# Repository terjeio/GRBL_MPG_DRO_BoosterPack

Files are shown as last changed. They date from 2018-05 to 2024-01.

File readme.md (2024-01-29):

## GRBL MPG & DRO BoosterPack for Tiva C \(TM4C123G\) and RP2040 (Pi Pico)

__2024-01-29:__ Added firmware and flasher code for the MSP430 keypad controller to the RP2040 version. This will check for and install/update the firmware automatically.  
Splitted LCD driver code in separate files for each display type supported.

__2022-01-13:__ Added wiring diagram for default key and LED map.

[Default wiring diagram (pdf)](media/Default%20keypad%20and%20LED%20wiring.pdf).  

The latest keypad code allows adding new keymappings at run time, switching between a few predefined ones or creating a new from scratch.

__2022-01-10:__ First preliminary version with Pi Pico support committed. Tiva C \(TM4C123\) version updated for new HAL/APIs.

__2021-08-30: Pi Pico breakout board design__

First batch of boards \(for final design verification\) to be ordered soon.

__2021-05-01: HALification of the code is underway__

A RP2040 driver for [Pi Pico](https://www.raspberrypi.org/products/raspberry-pi-pico/) is nearing completion, watch this space.

__2019-08-20: Improved startup sequence__

The GPIO line used for signalling MPG mode change is now used to signal the grbl controller ready state during startup.

On a cold start the Grbl microcontroller should pull the line low as early in the process as possible.
When the cold start sequence is completed and grbl is ready to receive data the line should be reverted to input mode with interrupt and pullup enabled.
The MPG microcontroller will wait for the line going high before starting any communication, displaying a progress indicator in its boot screen while waiting.

---

Features:

* SPI LCD and touch interface
* Up to two MPG wheels (QEI connected)
* Four GPIO pins, one is preassigned for switching grbl to/from MPG mode
* Up to 8 LEDs, buffered open drain 
* Feed Hold and Cycle Start outputs, open drain
* Up to 25 keys (in matrix)
* Navigator interface
* I2C port (3V3)
* On board MSP430G2553 handling keys and LEDs, internal I2C interface to Tiva C

Parts of alpha-version of supporting code is now available.
An initial commit of the [display driver](https://github.com/terjeio/Display-libraries/) used has now been made public.
The code is written so it is should be easy to port, all processor dependent code is in separate files. 

All core funtionality is now up and running, GUI is 100% event driven making it easy to extend with new dialogs. Shared dialogs (canvases) created for common data (such as DOC, feed rate, RPM), input review/confirmation and GCode transfer to grbl.

### How it works

The setup comprises 3 microcontrollers: one running Grbl, one handling the keyboard scanning and one (the MPG processor) for the DRO and MPG \(user interface\).

#### Grbl/grblHAL microcontroller:

Support for a second input stream and a switch for changing to/from MPG mode has to be added to the code.
In \"normal\" mode the MPG processor listen to the output stream from Grbl, parses the data and displays relevant info on the display.
In \"MPG\" mode Grbl switches its serial input to the second input stream and the MPG prosessor takes over control by acting as a GCode sender.
To tell the MPG processor about a mode change the real time report from Grbl is extended with |MPG:0 \(\"normal\"\) and |MPG:1 \(\"MPG\"\), this is only added when the mode change takes place.
Some of my [grblHAL drivers](https://github.com/grblHAL) supports this functionality as does my [patched version of grbl-Mega](https://github.com/terjeio/grbl-Mega).
 
#### MPG microcontroller:

This handles the user interface \(keypresses, MPG input, menu navigator input and DRO display\). In \"normal\" mode it passively listen to the output stream coming from Grbl, parses it and updates the display and LED statuses accordingly.
For this to work correctly there has to be a PC based GCode sender connected to the controller, such as [ioSender](https://github.com/terjeio/ioSender), that constantly request the real time status report.

In \"MPG\" mode it takes over control and acts as a GCode sender itself, ideally the PC based GCode sender should then disable its GUI.
When turning the MPG wheels G1 commands are issued with a feed rate that is dependent on the turning speed, simulating the action of the handwheels on the lathe.
The jog buttons issues jog commands and most of the other buttons issues real-time commands such as Hold or Cycle start. It is also possible to hardwire some of the button states to the corresponding Grbl input signals.

For the lathe version I am currently working on I am adding canvases \(or dialogs\) that will be used for some simple tasks such as reducing the diameter of the stock, and possibly threading if the Grbl version supports that.
There is a common canvas for streaming task data, this may be used to stream data from a SD card \(not yet implemented\). 

#### Keyboard handling microcontroller:

Due to limited IO on the MPG microcontroller a separate processor is employed for handling the keyboard and LEDs.
Up to 25 keys can be added (in a matrix) and 8 LEDs are supported. Keypresses are sent to the MPG controller via I2C, and there is a strobe signal for telling MPG controller that a key is pressed.
The strobe signal suppports different key modes such as single shot, autorepeat and continuous - configurable per key.

---

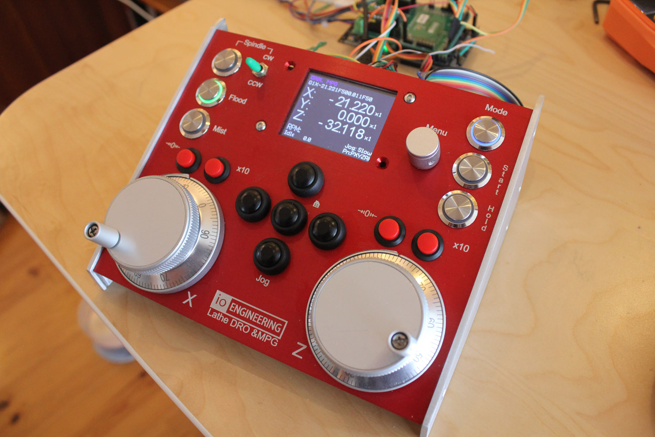
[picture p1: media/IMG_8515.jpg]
Testbench setup


### Pi Pico breakout board

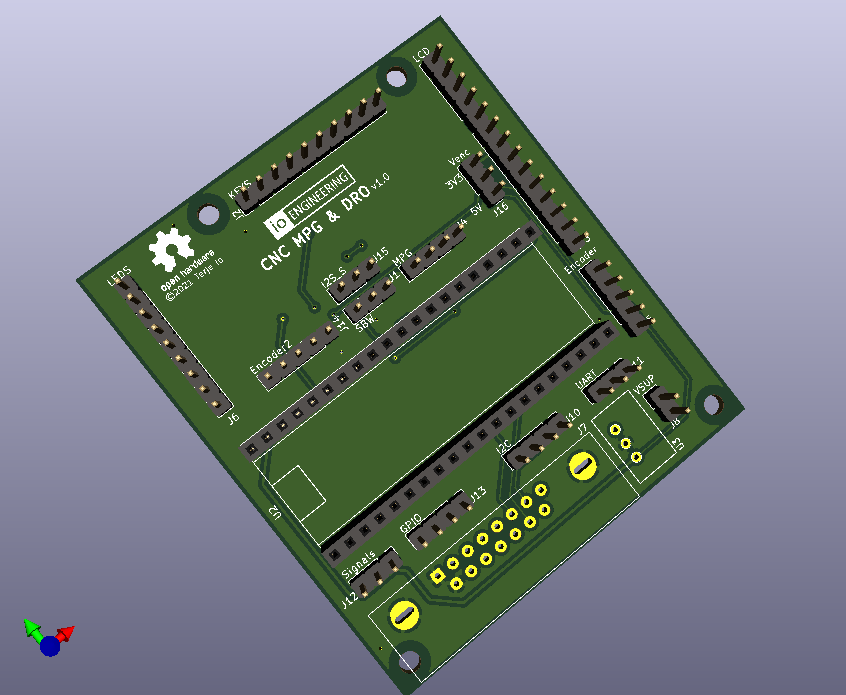
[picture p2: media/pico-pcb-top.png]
Pico PCB top

 
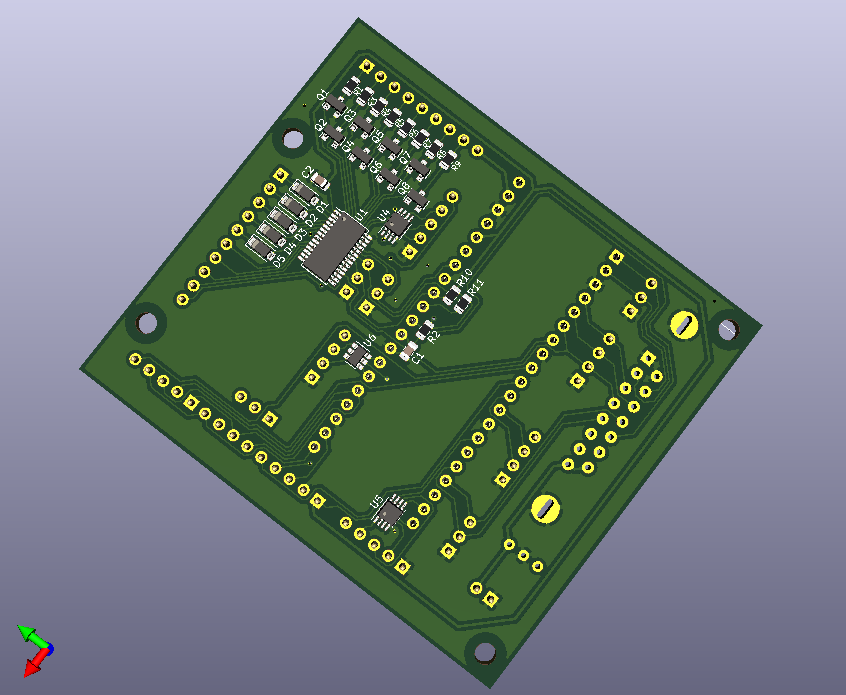
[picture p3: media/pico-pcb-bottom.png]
Pico PCB bottom


---
2021-08-30

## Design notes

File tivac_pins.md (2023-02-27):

#### LaunchPad pin assignments:

``` plain
                   3v3 [] [] VBUS (P14.1)                             PF2 [] [] GND
                   PB5 [] [] GND                         GPIO1 (P2.4) PF3 [] [] PB2 GPIO3 (P2.2)
    UART RX (P3.3) PB0 [] [] PD0 I2SCL (P10.3)           GPIO2 (P2.3) PB3 [] [] PE0 Cycle start (P8.2)
    UART TX (P3.2) PB1 [] [] PD1 I2SDA (P10.3)          Keypad strobe PC4 [] [] PF0 QEI0 (P6.3)
                   PE4 [] [] PD2 GPIO6 (P10.4)          QEI1 A (P9.3) PC5 [] [] RST
                   PE5 [] [] PD3 DISPLAY CS (P13.7)     QEI1 B (P9.2) PC6 [] [] PB7 MOSI (P13.4, P12.3?)
SCK (P12.5, P13.3) PB4 [] [] PE1 Feed hold (P8.3) Navigator SW (P5.4) PC7 [] [] PB6 SIMO (P13.1, P12.2?)
       D/C (P13.5) PA5 [] [] PE2 TOUCH CS (P12.4)   Navigator+ (P5.3) PD6 [] [] PA4
            I2CSCL PA6 [] [] PE3 TOUCH IRQ (P12.1)  Navigator- (P5.2) PD7 [] [] PA3
            I2CSDA PA7 [] [] PF1 QEI0 B (P6.2)           RESET (P13.6)PF4 [] [] PA2

GND: P2.1, P3.1, P5.1, P8.1, P10.1, P13.8
3V3: P5.5, P6.5, P9.4, P13.2, P13.9
 
```

#### Tiva connected socket/pins:

GPIO \(P2\):

```
GND   GND P2.1
GPIO3 PB2 P2.2
GPIO2 PB3 P2.3
GPIO1 PF3 P2.4
```

UART \(P3\):

```
GND GND P3.1
TX  PB1 P3.2
RX  PB0 P3.3
```

Navigator \(P5\):

```
GND GND P5.1
-   PD7 P5.2
+   PD6 P5.3
SW  PC7 P5.4
```

MPG0 \(P6)\:

```
GND GND P6.1
+   PF1 P6.2
-   PF0 P6.3
3V3 3V3 P6.4
```

Signals, open drain \(P8\):

```
GND         GND P8.1
Cycle Start PE0 P8.2
Feed Hold   PE1 P8.3
```

MPG0 \(P9\):

```
GND GND P9.1
+   PC6 P9.2
-   PC7 P9.3
3V3 3V3 P9.4
```

I2C \(P10\):

```
GND GND P10.1
SDA PD1 P10.2
SCL PD0 P10.3
IRQ PD2 P10.4 (I2C Strobe signal)
NC  --- P10.5
```

LCD Touch Sensor \(P12\):

```
T_IRQ PE3 P12.1
T_DO  PB7 P12.2 (MISO)
T_DIN PB6 P12.3 (MOSI)
T_CS  PE2 P12.4
T_CLK PB4 P12.5
```

LCD Display (P13):

```
SDO   PB6 P13.1 (MISO)
LED   3v3 P13.2
SCK   PB4 P13.3
SDI   PB7 P13.4 (MOSI)
D/C   PA5 P13.5
RESET PF4 P13.6
CS    PD3 P13.7
GND   GND P13.8
VCC   3V3 P13.9
```

---

#### MSP430G2553 connected socket/pins:

Keypad matrix interface \(P11\):

```
ROW0 P11.1  P1.0
ROW1 P11.2  P1.1
ROW2 P11.3  P1.2
ROW3 P11.4  P1.3
ROW4 P11.5  P1.4
COL0 P11.6  P2.0
COL1 P11.7  P2.1
COL2 P11.8  P2.2
COL3 P11.9  P2.3
COL4 P11.10 P2.4
```

LEDs, open drain \(P14\):

```
LED0 P14.8 P3.0
LED1 P14.9 P3.1
LED2 P14.7 P3.2
LED3 P14.6 P3.3
LED4 P14.5 P3.4
LED5 P14.4 P3.5
LED6 P14.3 P3.6
LED7 P14.2 P3.7
+5V  P14.1
```

SWD - MSP430 programming interface \(P4\):

```
GND  P4.1
TEST P4.2
RST  P4.3
```

---

#### Internal keypad interface to Tiva MCU:

```
P1.6 I2CSCL        PA6
P1.7 I2CSDA        PA7
P2.5 Keypad strobe PC4
```

---
2023-02-27

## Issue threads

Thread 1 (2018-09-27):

Congratulations!, great job!

luisluna2, 2018-09-27:
Hello friend just now I¿'m working in a similar project, but I wenna usa  a SD card but not have success with this.

I make  a code with LCD 1602 I2C and now the machine can move but the problem is how send data from SD CARD, have some about this?

terjeio, 2018-09-27:
Thanks,

Funny you should mention SD card now, I just looked into how to hook code for streaming data from a SD card into my grbl port a few hours ago. So far I just added the hook, no code yet for interacting with the card.

 I have also added added code (not yet published) for streaming GCode via ethernet to the driver for the [EK-TM4C1294XL LaunchPad](https://github.com/terjeio/grblHAL/tree/master/drivers/TM4C129), this ment that I had to run grbl as a FreeRTOS task - in a similar vein as the ESP32 port found [here](https://github.com/bdring/Grbl_Esp32). The ESP32 port support for streaming from a SD card, maybe that implementation can give you some ideas?

Do you use a second microcontroller for your solution too?

luisluna2, 2018-09-27:
wow! good job!, could send some picture for undertand more?, sorry I'm new in Arduino hehe

terjeio, 2018-09-28:
@luisluna2 I have added some details about my setup to the readme that may be helpful. Implementing the setup you describe on a single microprocessor is IMO not going to be easy, the Arduino Nano surely does not have enough free resources for that. Perhaps the way forward will be to use your Mega as the Grbl controller, this with my patched version, and implement the DRO/MPG and SD card support on the Nano?

I do not work with Arduino controllers, my expertise is with TIs 16 bit controllers and ARM processors, so I can not offer much help for Arduinos. Maybe switching to the ESP32 I mentioned above is a better choice for your ambitions, but it still needs a second processor for some parts (such as keyboard input) as it has limited IO resources. Or you could adapt this project if you feel so inclined...

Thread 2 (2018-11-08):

3 or 4 wheels

jschoch, 2018-11-08:
I'm working on a similar project but with 3 or 4 wheels.  STM32 can support 4 hardware quadrature pulse counters.  Wondering if this is something you have considered?  Also wondering how the physical interface is to use with your layout.  Any lessons learned on the physical UI?

terjeio, 2018-11-08:
Not sure what you mean, but I will try to answer.
I have not considered using STM32 processors, I mainly work with Texas Instrument processors. However, I try to write my code in a layered manner so that hardware dependencies are implemented in separate files from the main application - as a HAL (Hardware Abstraction Layer). This allows for clean porting to different platforms. If you meant support for more than 2 wheels then I have not considered that but it should be fairly easy to add to my code. It could also be done by a single wheel and an axis selector switch.

Again, not sure what you mean by lessons learned from the physical UI - you mean the complete layout with the LCD, MPG wheels, menu navigator and buttons? If so then I am happy with it as it is aimed at controlling my small lathe. It would be nice to have a complete numerical keypad for data entry - but that would result in a much larger device. So I decided to use a MPG wheel in combination with the jog buttons and meny navigator for data entry to keep the size down. One issue on my todo list is to change the input fields for numerical values to right justified - I need to update the UI library for that.
The LCD is touch sensitive and the UI library supports touch input, currently this is not enabled in my code, I will add that it later to see how it works out as an alternative to the menu navigator.

jschoch, 2018-11-09:
This helps.  I made a bad assumption you were using this for a mill style machine.

I want to have X, Y, Z, and Feed jog wheels all available.  X would be "front", Y "right", Z "top", and "feed" left laid out on a cube.

I was also asking about your hardware input device layout, how you like it, and what lessons you learned designing it.  Sounds like you are pleased with the  physical input layout for a lathe.  Could you use it for a mill?

terjeio, 2018-11-09:
> Could you use it for a mill?

Short answer: the physical design, no - the software yes.

For a mill I think I would reduce the design to a single MPG wheel and an axis selector switch - I believe this is the most common configuration for mills. But then your use-case may be different.

I like the jog buttons so I would add two for the Z-axis as I have done for my CO2-laser. The keyboard scanning code supports two-key rollover which I use for jogging X and Y simultaneously.

Perhaps a numeric keypad for data entry would be more useful than three MPG wheels? Depends on how advanced and easy-to-use one wants the software to be.

Whatever the physical design chosen I believe the core software can, IMO, be easily adapted to support it.

Using a MPG wheel for feed is perhaps an overkill, when in DRO mode I use the menu navigator for adjusting the spindle RPM, it could be used for feed as well. Be aware that when turning the MPG wheels I do not issue jog commands - I prefer to issue G1 commands with feed rate proportional to the turning speed to move the axes to the exact position as indicated by the wheel dial or the DRO. When turning the wheels the DRO position changes color to indicate target position is shown, not the current as reported by Grbl.

terjeio, 2018-11-11:
I use short key presses on the "Home key" in the center of the jog buttons to toggle between fast, slow and step mode jogging. In my GCode sender I use <SHIFT> and <CTRL> as jog modifiers in a similar way. Since I have (IMO) fixed the jog cancel "bug" I issue "long" jog commands in fast and slow modes and relies on the jog cancel command to terminate a running jog movement. This means that I do not rely on any feedback other than the current state for the action taken.

For the G1 commands I rely on the speed of the MPG wheel to calculate the feed rate - I get the velocity from a register in the processor. The formula to calulate the feed rate can be found in the source code (canvas/dro.c and mpg.c). The way I handle the MPG input is in a way a "set and go" mode as you describe it - in an interactive way. The target position is displayed in the DRO while a wheel is turned - also the dial (or scale?) on the wheel may be used, there is a button for aligning this dial with the DRO display.

Perhaps [this video snippet](https://www.youtube.com/watch?v=_0Nmh164dvo) may shed some light on how it works?

terjeio, 2018-11-11:
> The colored position is the cumulative target?

I guess you can say so, it is the absolute position where the controlled point (the tool) will stop if one stop turning the handwheel. It is still early days for me in terms of usage, so far I like to look at the DRO for approaching the target and then often the dial markings (or whatever they are called for) on the wheels for the final adjustment. I have started to write some canvases (or screens) for data entry for some simple tasks,  I guess that is nice to have for better surface finish and, for a mill, stuff that is hard/impossible to do manually but not complicated enough to warrant making a proper Gcode program.

>  Did you consider displaying both current and target?

Could do but so far I did not feel I need it, it is also a question of available screen real estate and avoiding clutter in the display. Also at x1 mode the controlled point does not lag much behind - turning a MPG wheel is kind of similar to turning a physical handwheel (that is my design aim). That said, I am no machinist - I am an electronics engineer/programmer making CNC stuff as a hobby so what do I know...
The nice thing about making my own design and writing the code is that I can change stuff to my liking :-)
>  If so why did you choose a single position display?

See above, may well change it later as the data is a few display calls away.

Having this discussion here is no problem for me, I - and others - may learn something from the discussion as well.

terjeio, 2018-12-03:
MPG wheels: bounce (if any) not an issue, I guess the QEI module in the processor takes care of any since I have enabled filtering by calling QEIFilterEnable. I have not tried with filtering disabled.

Menu navigator encoder:  bounces badly - added software debounce to fix that. RC-filters should help but I did not add them, slow opto-couplers can also act as debouncers. I have used MAX6816 for debouncing input to a CPLD in another project - a bit expensive but reliable, perhaps debounce duration is too long for an encoder? MAX6817 is the dual input version.

Optical encoders should IMO produce a clean signal, but may still cause bounce if the inputs are not schmitt triggered. Output from a optical encoder may in fact be considered analog if output is not preconditioned to be digital. Digital in this context meaning the output having a constant rise/fall time regardless of speed.

jschoch, 2018-12-06:
thanks for the response again.

I'm way down the rabbit hole on this now. I thought it would be much simpler but i'm learning a lot.

Right now i'm stuck deciding how to handle state transitions.  I think your code will calculate the delta to the target position and wait for that position to allow more input from the encoders.  Did you consider issuing the jog and then watching the states transition Idle -> Jog -> Idle?  I can see a possibility where I miss a transition and then never can accept new jog inputs.

 I suppose the only reason not to calculate the target position is some small saving in that calculation, perhaps I need to track these transitions to fully utilize CMD_JOG_CANCEL, but now that i'm thinking though the state transition monitoring I can't see any good reason it would be better with open loop control.  For closed loop there may be some reason you'd never get to the target position.  Wondering what your thinking was on when to block additional jog inputs.

I also generalized your grblcomm stuff into an arduino library here:  https://github.com/jschoch/grbl_chat
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
terjeio, 2018-12-06:
I issue "normal" G1 commands when movement is commanded via the MPG wheels, not jog commands - so there is no jog cancel involved.

What may be hard to infer from my code is that it is completely event driven. The EventNullEvent trapped in canvasHandler() in dro.c will happen every 10mS, I use that to flag when the display should be updated and the mpg input should be checked. Currently the display update is set to 20 ticks (200ms) and mpg input to 10 ticks (100ms).

In my main() function you will see it ends with 3 calls in a while(true) loop, the those calls would go in the loop() function if the same approach was used for Arduino.

MPG_Move() thus gets called every 100ms, which gets MPG wheel positions from the QEI module and compares them to a local copy, if different the delta is computed and used for calculating the target position.

I do not rely on state transitions from grbl to handle MPG movement, as long as the wheels are turned I will issue G1 commands (every 100mS). A state change back to "normal" is when there was no change in MPG positions during the last 100mS period.

To be able to do this I need to set a reference position (current position from grbl, mpg_base), to update this I rely on a state change to Idle - see displayGrblData() where I call MPG_ResetPosition(). Also offset changes is taken care of as well as setting the reference position at startup.

How this could be adapted to issue jog commands instead in a good way I do not know. Do you just want to continue issuing jog commands until wheel movement stops and then issue a jog cancel? Or only cancel on a direction change?

As for the "bug" in parseFeedSpeed that is due to I change I have made to the real-time report, I have added a third parameter - the actual spindle speed.  This one should work:

```
static void parseFeedSpeed (char *data)
{
    char *next;

    next = strchr(data, ',');
    *next++ = '\0';

    if(parseDecimal(&grbl_data.feed_rate, data))
        grbl_data.changed.feed = true;

    if(parseDecimal(&grbl_data.spindle.rpm_programmed, next))
        grbl_data.changed.rpm = true;

}
```

I hope this helps, if not just continue asking.

jschoch, 2018-12-06:
thanks again, this is great feedback.

> How this could be adapted to issue jog commands instead in a good way I do not know. Do you just > want to continue issuing jog commands until wheel movement stops and then issue a jog cancel? Or > only cancel on a direction change?

The two modes i'm considering are single step, and acceleration based "batch step".  The latter might benefit from jog_cancel since I want to have the grbl planner accelerate based on the wheel velocity and time it has been turning.  My idea was to mark the wheel turning with a flag when it starts turning and then if the wheel had been turning and stopped to issue the jog_cancel and to halt all other input to grbl.  I see that folks try to just stop issuing more jog commands rather than trying to use CMD_JOG_CANCEL due to the potential race condition.  I've not yet been able to get something that works smoothly and avoids odd states and I'm actually focused on getting the first cast working safely and atomically.

Right now I'm processing the encoder wheel updates very quickly (by mistake) and I likely am creating more problems for my self that way.  The current version issues a "?" query after the jog and I notice that I can issue and receive "ok" for 2 or 3 jog commands before the state changes to a Jog state.  reducing  encoder wheel input polling time is a pretty easy way to get more control over things.

my next refactor will try to model things based on a finite state machine.  I will pay closer attention to polling intervals and start to calculate target positions.

Closed 2020-02-04.

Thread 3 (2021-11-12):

Possible to buy an PIPico pcb?

mundsen, 2021-11-12:
Cool project

terjeio, 2021-11-13:
I have to order some PCBs first - been too busy to do that. I have one homemade prototype (single-sided) so hopefully the first run will be bug-free...

mundsen, 2021-11-13:
ok :-)

Have ordered a Tiva C , LCD and Pico

As a first step I hope to get the LCD working in combination with my grblHAL Pro

terjeio, 2021-11-13:
The Tiva C is not needed, the Pico is used as an alternative...

There is a MSP430 on the board that needs to be programmed, my plan is to port the programming code (it is public domain) so that the Pico can do that.
Currently I use a MSP-EXP430G2 to program it, it is possible that the Tiva C can be used as well. Anyway, I believe can supply a preprogrammed MSP430 - IIRC I have an adaptor for doing that off PCB.

terjeio, 2022-01-05:
FYI I have now received a few PCBs and have the first up and running with basic functionality in place.
I need to make a 5x5 keypad to assign and check out new key mappings required as the board only support a single MPG encoder so there is a little bit more work to do before I can release the code.

You still want a PCB? Unpopulated?

mundsen, 2022-01-05:
Yes 😊

Would like to test it with my laser project based on the grblHAL Teensy 4.1 Pro controller [Image.jpeg]

Last ned Outlook for iOS<https://aka.ms/o0ukef>
________________________________
Fra: Terje Io ***@***.***>
Sendt: Wednesday, January 5, 2022 9:07:33 PM
Til: terjeio/GRBL_MPG_DRO_BoosterPack ***@***.***>
Kopi: Øyvind Amundsen ***@***.***>; Author ***@***.***>
Emne: Re: [terjeio/GRBL_MPG_DRO_BoosterPack] Possible to buy an PIPico pcb? (Issue #3)

FYI I have now received a few PCBs and have the first up and running with basic functionality in place.
I need to make a 5x5 keypad to assign and check out new key mappings required as the board only support a single MPG encoder so there is a little bit more work to do before I can release the code.

You still want a PCB? Unpopulated?

—
Reply to this email directly, view it on GitHub<https://github.com/terjeio/GRBL_MPG_DRO_BoosterPack/issues/3#issuecomment-1006040344>, or unsubscribe<https://github.com/notifications/unsubscribe-auth/AAXKXEKX45N3P5TTZ366LMDUUSQILANCNFSM5H47LWKA>.
You are receiving this because you authored the thread.Message ID: ***@***.***>

mundsen, 2022-01-08:
Is Grbl v1.1 jogging supported by grblHAL ?

https://github.com/gnea/grbl/wiki/Grbl-v1.1-Jogging

terjeio, 2022-01-08:
> Is Grbl v1.1 jogging supported by grblHAL ?

Yes, and I have fixed the bug where a jog cancel is sometimes not handled as it should.

Also, legacy Grbl errors out if a jog command exceeds max travel if soft limits is enabled - contrary to what the linked document claims. grblHAL has separate soft limits handling for jog commands that can be enabled by setting $40 to 1.

terjeio, 2022-01-13:
Testing is going well and I have ordered an adaptor for programming the MSP430 off board. Should be here soon.

Here is the BOM as extracted from KiCad:

[RP2040 MPG and DRO.zip](https://github.com/terjeio/GRBL_MPG_DRO_BoosterPack/files/7860577/RP2040.MPG.and.DRO.zip)

R1-9 has no value due to LEDs often having different current requirements for outputting the same brigthness. I use 2K7 for the 3mm LEDs in my test setup and the different colors vary from quite dim to very bright...
R1-9 could be replaced with 0R resistors on the board and having leaded resistors in series with the LEDs instead.

U3 is not needed if the supply voltage is 5V or the Pico is connected via USB. Short pin 1 and 3 with a wire if so.

DB15 is optional, use the connector(s) of your choice and wire to the pin headers as needed. I believe that wireless operation via HC-05 bluetooth modules is possble but I have not tested that yet.

The display is a [2.4" ILI9341 based panel](https://www.ebay.co.uk/sch/i.html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), I may add touch support later but not sure if it is going to be practical.

My test setup has all 25 buttons wired up, do you plan to add any? ([You will need at least two](https://github.com/terjeio/GRBL_MPG_DRO_BoosterPack/discussions/6#discussion-3786872)).

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

mundsen, 2022-01-13:
Possible to use something like this?

https://www.aliexpress.com/item/32635207928.html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,scm-url:1007.13339.169870.0,pvid:af4624f1-85fd-40f5-8538-35733463f9a3,tpp_buckets:668%232846%238111%231996&&pdp_ext_f=%7B%22sceneId%22:%223339%22,%22sku_id%22:%2210000006002568188%22%7D

less wires - Seems like different keys gives different ohm values?

terjeio, 2022-01-13:
> Possible to use something like this?

Yes, but you will have to write code for it. Polling an AD-converter and decoding the value. You can ditch the MSP430 if doing that - and luckily the I2C SDA/SDC going to it are broken out to a pin header. Depending on how many key functions you require it may be a bit restrictive though - and I am not sure you will be able to get two key rollover to work.

mundsen, 2022-01-13:
Ok only an idea - I guess it’s best start with the same setup you use

Last ned Outlook for iOS<https://aka.ms/o0ukef>
________________________________
Fra: Terje Io ***@***.***>
Sendt: Thursday, January 13, 2022 10:01:49 PM
Til: terjeio/GRBL_MPG_DRO_BoosterPack ***@***.***>
Kopi: Øyvind Amundsen ***@***.***>; Author ***@***.***>
Emne: Re: [terjeio/GRBL_MPG_DRO_BoosterPack] Possible to buy an PIPico pcb? (Issue #3)

Possible to use something like this?

Yes, but you will have to write code for it. Polling an AD-converter and decoding the value. You can ditch the MSP430 if doing that - and luckily the I2C SDA/SDC going to it are broken out to a pin header. Depending on how many key functions you require it may be a bit restrictive though - and I am not sure you will be able to get two key rollover to work.

—
Reply to this email directly, view it on GitHub<https://github.com/terjeio/GRBL_MPG_DRO_BoosterPack/issues/3#issuecomment-1012512387>, or unsubscribe<https://github.com/notifications/unsubscribe-auth/AAXKXEIHS5A42XJA5XKE7RDUV44T3ANCNFSM5H47LWKA>.
You are receiving this because you authored the thread.Message ID: ***@***.***>

mundsen, 2022-01-20:
Does/can the LCD show other live status information when not in MPG mode ?
Job %
Alarm messages
Use some of the buttons for functions like CycleStart, Feed Hold..?

terjeio, 2022-01-20:
> Does/can the LCD show other live status information when not in MPG mode ?
Job %
Alarm messages
Use some of the buttons for functions like CycleStart, Feed Hold..?

I have not (yet?) implemented Job % (only available when running code from SD card), the rest - yes.

carneeki, 2022-01-20:
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

Is it running from the grbl SD card? If not, is there enough room to show current, and last couple of lines executed?

mundsen, 2022-01-20:
I have the PI, LCD..
Have to buy som eresistors..
So almost ready for the pcb :-)

terjeio, 2022-01-20:
> Is it running from the grbl SD card? If not, is there enough room to show current, and last couple of lines executed?

Currently any SD card has to be connected to the controller, not to the MPG. To display lines in the MPG they have to be transferred somehow. That would require code changes in the controller. It would be easier to add a SD card interface to the MPG board?

> So almost ready for the pcb :-)

And I am waiting for the TSSOP programming adapter, should be here any day now.

terjeio, 2022-01-29:
The adapter is here and I have a PCB and a preprogrammed MSP430 ready. Email terjeio@online.no for exchanging details.

mundsen, 2022-01-30:
Sent e-mail :-)

mundsen, 2022-03-22:
All parts arrived + a hot air soldering sation..

Hope to get some spare time soon - so I can get this pcb ready

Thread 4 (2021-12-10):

LCD for grblHAL (Teensy)

mundsen, 2021-12-10:
Hi
I order this [](https://www.waveshare.com/wiki/Pico-Eval-Board)
so I can use it to learn programming the pico

Can I use this with the code you use to display the grbl info in the LCD in this projct?

terjeio, 2021-12-10:
Not without either adding host mode USB support to the grblHAL driver or wiring UART TX from the Teensy to GP1 (which would require you to cut the connection to the CP2102 - by trimming the Pico GP1 pin off?).

Parts of my code can be used, perhaps only the [parser](https://github.com/terjeio/GRBL_MPG_DRO_BoosterPack/blob/master/Firmware/MPG%20and%20DRO%20processor/grblcomm.c) as it may be easier to use driver code already available for the attached display to display what you want.

Then the output stream from the Teensy has to be duplicated to the UART port if connecting via USB or Ethernet, I have changes coming which will make that easier - either via a simple plugin or a compile time definition.

I have to get the Pico MPG board sent off for manufacturing. Too little time for all I want to do...

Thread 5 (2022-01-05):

PiPico Board screw hole

carneeki, 2022-01-05:
Hi Terje,

In the PCB layout the J7 (controller) connector obscures a 3mm mounting hole (see first and second picture)
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

By rotating the VSUP header, and moving U3 further to the right, room can be made for both the screw hole and J7 (see third picture)
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

Also suggest using a 3.2mm hole; as it permits a #10-32 screw for those in the US.

I am hesitant to send a PR as I upgraded to KiCAD 6 and the files are not backward compatible (only forward compatible).

terjeio, 2022-01-07:
It is likely that I will change the D socket to a smaller version or replacing it with different connector(s). The latest version of the firmware I am working on can work with only four wires, or soon maybe even two (for power, with wireless transmission of data) or none (if battery operated).

What is more interesting is a discussion about how to connect to the controller and which kind of enclosures could be used. From that a more appropriate PCB design can be made.

FYI I made a 5x5 keypad yesterday for testing, and I have more than 30 commands assigned already. It seems like this can be a powerful/flexible platform to build upon...

carneeki, 2022-01-07:
Funny you mention enclosures, I am in the middle of designing one now that a friend offered to 3d print for me. My constraints are a 180x180 bed area.

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

I admit to going overkill with the screws, but that was an aesthetic choice ;)

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

The connector will likely be a CX20 or CX24 style connectors with a short pigtail from connector to board. (if you opt for 0.1" headers, that would permit a wide variety of connection options, including many cable to board connectors). CX24 permits up to 26 pins in and out of the enclosure (3A per pin) and I have found them quite cheap on AliExpress. Currently thinking:

- 15 pins for the MPG/DRO board to main controlbox (currently Pi3 + Grbl, stepper drivers, 5V, 12V and 48V PSUs),
- 2 pins for 5V/12V power and I have a number of spare lines I can use in the future.
- 9 pins free for future use

I haven't put a display or buttons in yet; one idea that I thought about was to use buttons next to the display similar to what many oscilloscopes offer. The buttons can be assigned different tasks depending on the screen you are looking at. Here is a spectrum analyser I've used, the 5 buttons below the screen are redefineable "soft" buttons:

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

Fluke 289 multimeter does this too:

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

Having, a few buttons at the bottom and the sides would open up many options for users interacting with the device. As I'm not sure what sort of displays you are planning to use, I was actually in the middle of looking your different repos to see if I could figure it out when you replied :)

My enclosure is probably far bigger than what most MPG pendants opt for, but something like this enclosure might suit the 5x5 keypad and the MPG wheel, with room for a few soft buttons too:

https://www.thingiverse.com/thing:2218467

mundsen, 2022-05-15:
I'm going to start on mine (solder the smd components on the pcb..  Anyone have one up and running that want to share images.. for inspiration?

mundsen, 2022-05-15:
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

in the grblhal2000 Jog2K pendant project, they use an USB-C fron the pendant to the controller

terjeio, 2022-05-17:
> in the grblhal2000 Jog2K pendant project, they use an USB-C fron the pendant to the controller

If I am not mistaken a Pi Zero acts as a USB host to UART comms translator between the controller and the pendant.

andrewmarles, 2022-05-17:
> r

No, it is more simple than that.  The Jog2K uses a just a Pi Pico to emulate an I2C keypad to GRBLHAL.  The USB-C connector is just a physical interface that is convenient because it is compact, surface mounted and has enough conductors for KPSTR and e-stop as well as differential I2C (in the original implementation).  All of the communication is I2C, including the addition of DRO and status display.

I have not created a PR for the keypad code as it is kind of its own thing for the jog2k and Hal2K since the hardware is slightly bespoke.  But I am happy to formwat it as such if you are interested to take a look  Also I have plans to find a way to run a modified version your own MPG/DRO firmware on the jogger instead of my current code as I would prefer that the two projects converge rather than diverge, but sadly time is not infinite so I have not gotten to that yet.

andrewmarles, 2022-05-17:
Having said all that, I went ahead and created the PR in case it is useful.

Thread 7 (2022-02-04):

Can you share the pcb 3d model?

mundsen, 2022-02-04:
as a step file?

terjeio, 2022-02-04:
[RP2040 MPG and DRO.zip](https://github.com/terjeio/GRBL_MPG_DRO_BoosterPack/files/8006051/RP2040.MPG.and.DRO.zip)

mundsen, 2022-02-04:
Thank you - did add image on each side and a pi pico from grabcad :-)

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

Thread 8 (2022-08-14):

MPG Project Status?

ThatGuy435, 2022-08-14:
I'm not sure if there's a better way to inquire about the current status of this project, but where does it stand as of August 2022? Are the published PCBs working, and are there ways to program the MSP430G2553 without having the specific programming hardware?

terjeio, 2022-08-15:
> Are the published PCBs working

Yes, but consider them reference designs - and go for the Pi Pico version.

>  and are there ways to program the MSP430G2553 without having the specific programming hardware

Not yet, my longer term plan is to add code to the Pi Pico for programming the MSP430. And I can supply a preprogrammed MSP430 if of interest.

The MSP430 _can_ be replaced with another MCU, e.g. an Arduino compatible one, but again I do plan to do that - I have had enough of the so-called Arduino IDE...

ThatGuy435, 2022-08-15:
Awesome!

I'm in the midst of a conversion of a mini mill with one of Phil Barrett's GRBLHal teensy boards, and was hoping to be able to use it more or less like a manual for stuff like squaring up stock and other faster-without-programming operations. It seems like this MPG would give that functionality.

Is the JTAG programming interface for the MSP430 broken out on the board anywhere, or do I need an entirely separate programming board? Alternatively, what is the recommended hardware for flashing that chip? I'd probably rather have the equipment on hand to reflash myself in case I blow it up at any point.

terjeio, 2022-08-15:
The JTAG interface is not brought out, the SWD is. You can use a [MSP430 LaunchPad as a programmer](http://www.msp430launchpad.com/2011/10/programming-devbo-and-external-targets.html), see the end of [this readme](https://github.com/terjeio/PCBLaserFirmvare#readme) for how to compile. I do not know if a J-Link or similar can be used.

[Here is another link](https://www.yuriystoys.com/2013/09/how-to-upload-firmware-to-msp430.html) detailing how to program.

ThatGuy435, 2022-08-15:
Awesome, thank you for the assistance!

runryder912, 2023-03-03:
> The MSP430 _can_ be replaced with another MCU, e.g. an Arduino compatible one, but again I do plan to do that - I have had enough of the so-called Arduino IDE...

What kinda of funding do you need to help push this forward?

terjeio, 2023-03-03:
> What kinda of funding do you need to help push this forward?

Enough to hire somebody to do it? But then I do not know anybody who is familiar with the Arduino framework...

As I wrote above it is on my todo list to add code to the Pico so it can program the MSP430 from code embedded in the Pico flash, I'll rather get around to do this than spend more time on a programming framework that drives me nuts.

If you really want the code ported it will be far better to find someone whith experience with the 8-bit Arduinos, and there are likely projects out there that can be used as references - or with luck, more or less as-is.
The basic spec is quite simple: scan a key matrix<sup>*</sup> and make a byte available to be collected via I2C when keys are pressed.
However, implementation is, IMO, not entirely trivial. Key debounce has to be implemented, and the different keypress modes as well. Short keypress, long keypress and key up/key down signalling - all via a single strobe output to interrupt the I2C master. Two-key rollover is nice to have but not required.

<sup>*</sup> If the MCU has enough input pins to support the keys required using a matrix is not a requirement. Or matrix scanning/key input can be done on the Pico itself, again provided that there are enough free pins.

M10CUBE, 2023-03-24:
Sorry  @ThatGuy435 for hijacking  your space but looks the correct place to place an idea that will profit our community here and give a boost the excellent job made by @terjeio .
One year ago I had an idea of designing an MPG PENDANT (more simplified that this fine piece designed by @terjeio )
After reading this thread I am wondering...
@terjeio on the Pi_Pico_Board what about substituting the MSP430 with another Pico module? Keeping all the user interface peripherals as is. Simplifies final user programming and have less cost.
In fact making the board a bit bigger (90X90 mm) can accommodate the 2XPICO. M10 PCB framework can be used . The build can have all the connectors ready for plugging with the framework already in the GRBL_MPG_DRO_BoosterPack (keyboards, switches, LCD etc)
It is obvious then to send data via WiFi to GRBLHAL as an option (later on when we have some free time)
I can help with the hardware if you can help with the firmware. May be more contributors may help on that
I for some reason feel that this post has no meaning please forgive and ignore it.
Thank you

terjeio, 2023-03-24:
>  what about substituting the MSP430 with another Pico module?

Better to use a RP2040 chip? BTW I have started porting code for programming the MSP430 from the Pico - automatically. I want to see if I can manage to do this before porting the code to another processor.

M10CUBE, 2023-03-24:
>
> Better to use a RP2040 chip?
>
Well it is a thought but my experience says that quickest and fastest way to bring a product in the "market" is to use the ready modules mass produced. Your Nucleo breakout CNC board is an excellent example. That is if you have the real estate on board and the module have all the pins from the MPU to the edge.
Looks that Pico has almost all pins on the edge (chip has 2 more pins I think).
If you allow me, I can make a rough idea of the design examining 2 scenarios using the 2X Pico modules.
I will try to imitate it in hardware with the second Pico  what you did with  MSP430 chip.

In fact all the pin-outs to the Picos will be as a direct replacement of the Pi_Pico_Board.
All you have to do is upload to 1st pico the code already there and port MSP430 code to the 2nd Pico

That hardware can be implemented very easily and fast
In a later time If we feel confident we can recreate everything on a new board using 2xRP2040 chips and porting the same code.
Thanks to KiCAD 7 (now)
>
>BTW I have started porting code for programming the MSP430 from the Pico - automatically. I want to see if I can manage to do this before porting the code to another processor.
>
Yes I sow that in a previews post. Go for it. Meanwhile i will study the Pi_Pico_Board preparing the 2 solutions I am thinking.
So please I like to here about that.

terjeio, 2023-03-28:
> Well it is a thought but my experience says that quickest and fastest way to bring a product in the "market" is to use the ready modules mass produced.

That depends on whether you indent to have the board ready made or components soldered by the buyer. If ready made it will be easier to have the chip(s) presoldered. Like [this pendant](https://github.com/Expatria-Technologies/RT_Jog_Controller).
For the RP2040 it will still be an issue for how to program the keypad controller chip though.

M10CUBE, 2023-03-28:
> That depends on whether you indent to have the board ready made or components soldered by the buyer. If ready made it will be easier to have the chip(s) presoldered.
>
Both have advantages and disadvantages. Considering that there is not going to construct thousands of boards
I will try to write here some but lets correct them in the process.
**Pico module advantages**
Ready of the self. Highly available. Can be used for other projects. Ready WiFi or Ethernet  available. Cheap and easy DIY construction and fast to market time. As an option user can provide his own Raspberry Pico from his stock
**Pico module disadvantages**
More real estate on  the mother board. Some pins are missing on the edge of the module (but used in favor of the WiFi chip).
Time needed to solder or to plug in the module.
More expensive than using the discreet components ?
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
terjeio, 2023-03-29:
> Is this a problem?

A RP2040 module is simple to program via the inbuilt bootloader that exposes it as a flash drive - just drag&drop the binary.
If using a RP2040 chip for the keypad processor it has to get its own USB connector (and boot button) to allow this, if not it has to be programmed via the SWD interface.

> I am already trying to make one new design (only schematic on KICAD7) coping and pasting from your GRBL_MPG Pi_Pico_Board to see what can be done. If revised and agreed we will go to design the PCB.
Is that OK?

Yes. But be aware that I have plans for a new version that aims to support two MPG encoders and a SD-card, this by removing the I2C keypad interface and some GPIO lines (to the controller). And possibly a variant that would support larger displays with a parallell interface.

M10CUBE, 2023-03-29:
>
> A RP2040 module is simple to program via the inbuilt bootloader that exposes it as a flash drive - just drag&drop the binary. If using a RP2040 chip for the keypad processor it has to get its own USB connector (and boot button) to allow this, if not it has to be programmed via the SWD interface.
>
Thus the idea of using the Pico module in the first attempt it will has as a bonus easy firmware downloading. That goes to advantage for the Pico module vs the discreet MPU
>
> Yes. But be aware that I have plans for a new version that aims to support two MPG encoders and a SD-card, this by removing the I2C keypad interface and some GPIO lines (to the controller). And possibly a variant that would support larger displays with a parallel interface.
>
Nice to hear that. it means we are moving forward.
Look @terjeio . To me it is just an hour of coping and pasting your module to find out here we stand at this point having 2XPico on board. Thanks to Kicad. No PCB routing.
Then your additions will come alive when ready.
Having the two designs in KiCAD schematics, it will be easy to have a mixture of the two. You can post your progress here or elsewhere if you like. In a new thread maybe?
To be honest last year as you know we proposed with Olivier in the WIZnet's  contest the Pico CNC board as well. There we had an early view of the pendant (called it remote control).
In fact a prototype have been constructed and Olivier wrote some firmware for the keypad and display. But as he [Volksolive](https://github.com/Volksolive) has no contact anymore the project abandoned. Petty I am worrying what happened to him. I hope he is just fed up with the project and nothing else. He just vanished.
Attached is the "abandoned" project I have in my lab and the KiCAD schematics. As I said only keypad and LCD is working.
That was an attempt to mimic the commercial ones "one hand holding" modules but having advanced hardware on it.
images are just for inspiration since as said having partly build one prototype the idea stalled.
Firmware done so far by @Volksolive can be posted as well.
In real life photo is the prototype using the Pico Wiznet Ethernet, TCP/IP modbus communication (green cable). The flat cable is for power. The idea was to have POE as well. But Wifi is better with 2x18650 batteries.
Only one Pico used as can be see from schematics but if we need more functions a second can be used since we will run out of pins.
A final note on our design. We had in mind to build a modular system. The module carrying the keyboard and the LCD could be used as a general purpose HMI in a home Automation system or elsewhere. Adding the encoder PCB can be used as an MPG.
Building blocks to to other jobs as well. A "Lego" concept. Saving the planet that way with a reusable modules.
What about that "green" idea? Can you inspired?
Having said that I think cooperating and contributing something nice will came out. ASAP
let us enjoy the ride
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
[M10HM01-19.pdf](https://github.com/terjeio/GRBL_MPG_DRO_BoosterPack/files/11099717/M10HM01-19.pdf)
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
[M10HM02-19.pdf](https://github.com/terjeio/GRBL_MPG_DRO_BoosterPack/files/11099724/M10HM02-19.pdf)
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

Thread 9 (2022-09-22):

MSP-EXP432P401R serial port not working

CHTUZKI, 2022-09-22:
HI.
I want to try this project. I bought a MSP-EXP432P401R board and compiled the project. But the serial port of my board doesn't seem to work, I can't communicate with my MSP-EXP432P401R board using iosender, I use the virtual serial port of the onboard XDS110. I don't know what the problem is, can you help me

terjeio, 2022-09-22:
> I can't communicate with my MSP-EXP432P401R board using iosender

The firmware is for communication with a grblHAL controller with MPG mode enabled, you cannot connect ioSender to it...

[PB0/PB1](https://github.com/terjeio/GRBL_MPG_DRO_BoosterPack/blob/master/tivac_pins.md) is used for connecting to the CNC controller MPG UART port.

CHTUZKI, 2022-09-23:
Sorry, there is something wrong with my question.
I now use the MSP-EXP432P401R board to run the GrblHAL firmware and then the Tiva board to run the GRBL_MPG_DRO_BoosterPack firmware. I think that the iosender communicates with the first serial port of MSP-EXP432P401R, and the Tiva board communicates with the second serial port of MSP-EXP432P401R. Is this the case? If it is my iosender can not communicate with MSP-EXP432P401R.

terjeio, 2022-09-23:
Ok, then you are using the boosterpack map and have no EEPROM connected? If so set [these two symbols](https://github.com/grblHAL/MSP432P401R/blob/063abf7af633c9159a36b34d10b5c7ca2bd86276/cnc_boosterpack_map.h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) to to 0 as the controller will hang if no EEPROM is present.

CHTUZKI, 2022-09-23:
I'm using the MSP-EXP432P401R board, which doesn't have any external expansion boards connected.

Below is my setup:
```
#define MPG_ENABLE          1
#define KEYPAD_ENABLE      0

#define CNC_BOOSTERPACK  1
#define I2C_ENABLE                0
#define EEPROM_ENABLE       0
```

But the problem still exists. iosender cannot communicate with grblhal through the virtual serial port of XDS110.

terjeio, 2022-09-23:
Even after changing the symbols?

CHTUZKI, 2022-09-23:
yes

CHTUZKI, 2022-09-23:
I checked the pins of the board with a multimeter and there is no problem

terjeio, 2022-09-23:
Ok, if you have downloaded the code with CCS can you stop execution with the pause button? Where does it hang?

And have you removed the jumpers connecting RXD and TXD between the debugger part of the board and the MCU part? You should not.

CHTUZKI, 2022-09-23:
I feel like the program is running normally, and I'm stepping through it. I put a breakpoint in the serial port interrupt function and I open iosn
`void SERIAL_IRQHandler (void)`
I feel that the serial port has no way to receive and send normally。
I'm going to compile an example now to verify that my board's serial port is OK.

terjeio, 2022-09-23:
I am running this driver with a CNC Boosterpack in my physical test machine, it has a 2K EEPROM and is running flawlessy. I just hooked up a spare board without anything connected (and EEPROM support disabled in the board file) and this starts too, albeit in Alarm mode since no pins are connected.

Note that this driver does not have support for saving settings in flash, either connect an EEPROM or hard configure it by uncommenting and editing definitions in _grbl/config.h_. Settings _can_ be changed at run time but will be lost on a hard reset.

CHTUZKI, 2022-09-23:
Thank you for your reply. I don't feel anything wrong with grblHAL now. Although my board still doesn't work. I'm not using CCS IDE, I'm using PlatformIO IDE, I found it might be the IDE's problem. I put a breakpoint on serialWriteS and in debug mode it prints out the characters, if I exit debug mode there is a problem.
I have had this problem many times with platformio, not only with MSP432, but also with STM32. It is possible to run step by step in debug mode, but not to exit debug mode. I will report the problem to platformIO.
I can't use CCS IDE because my chip may be pirated, and I can't upload programs using CCS IDE. I will buy another chip and retest.
Thank you very much~

CHTUZKI, 2022-09-25:
I replaced a brand new msp432p401r chip and downloaded it using CCS IDE without any problem. Everything works fine now.
I think it should be a problem with pirated chips or a problem with platformIO.

Thank you very much for your help. Thank you also for contributing such a cool project.

Closed 2022-09-25.

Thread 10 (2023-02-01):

identifier "KEYPAD_STREAM" is undefined

CHTUZKI, 2023-02-01:
`#define MPG_ENABLE          1

 #define KEYPAD_ENABLE      2`

I used the above two lines of code to compile, and the compiler told me "identifier" KEYPAD_STREAM "is undefined". I can't find "KEYPAD_STREAM" in the "MSP432P401R-master" project

I don't know why?

terjeio, 2023-02-01:
Those two symbols are for the grblHAL controller, which driver are you compiling for that?

Closed 2023-02-02.

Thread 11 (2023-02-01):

Can't run this project

CHTUZKI, 2023-02-01:
I want to run this project, but I have a lot of problems。

I use TM4C123GXL board as MPG controller，I use EXP432P401R board as grblhal controller,The source code of the grblhal controller is https://github.com/grblHAL/MSP432P401R.

I found that my MSP432P401R can't communicate with TM4C123GXL, I use a logic analyzer to measure the P3.2 and P3.1 pins of MSP432P401R, they don't have any data.（I use IOsender to communicate with MSP432P401R, and then use a logic analyzer to measure P3.2 and P3.1 pins，I think PC will give G code to MSP432, then MSP432 will use P3.2 and P3.1 pins to TM4C123. I don't know if I understand correctly）

My MSP432 board does not use EEPROM, I saw that this board can communicate with IOsender。

I debug MSP432 board and I found that
`if((hal.driver_cap.mpg_mode = stream_mpg_register(stream_open_instance(MPG_STREAM, 115200, NULL), false, NULL)))
        protocol_enqueue_rt_command(mpg_enable);`

will not execute。

I found in "cnc_boosterpack_map.h" file
`#if MPG_MODE == 1`
`#define MPG_MODE_PORT           port(C)`
`#define MPG_MODE_PIN            2 // GPIO2`
`#endif`

Does MPS432 have portC port? (GPIOC? GPIOC2?)

This is a great project and I want to run it, can you give me some help.

Sincere thanks.

terjeio, 2023-02-01:
> My MSP432 board does not use EEPROM

Have you changed the value in these lines in the map file from 1 to 0 to disable the EEPROM? If not the controller may hang.

```
#define I2C_ENABLE       1 // Only change if BoosterPack does not have EEPROM mounted
#define EEPROM_ENABLE    1 // Only change if BoosterPack does not have EEPROM mounted
```

When I try to compile the grblHAL driver I get a linker failure, solved by adding:

```
#if KEYPAD_ENABLE
#include "keypad/keypad.h"
#endif

```
after the EEPROM enable include in _driver.c_ (near line 45).

>Does MPS432 have portC port? (GPIOC? GPIOC2?)

Yes, the ports can be referenced both by numbers or letters.

CHTUZKI, 2023-02-01:
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

CHTUZKI, 2023-02-01:
`#define CNC_BOOSTERPACK`
`//#define I2C_ENABLE`
`//#define EEPROM_ENABLE`
`#define MPG_ENABLE 1`

Here is my configuration。

I don't think my MSP432 board is hanging. I am iosender and can communicate with MSP432.

I don't understand why the P3.2 and P3.1 pins of the MSP432 board don't have any data output。

terjeio, 2023-02-01:
Another "bug"...

Add  `serialRegisterStreams();` at line 1630 or so in driver.c (just before the driver cappabilities comment). At least this gives me serial transmit interrupts on Serial2...

CHTUZKI, 2023-02-02:
After adding the `serialRegisterStreams();` line, the system works normally。

🎉🎉🎉🎉thank you very much

Closed 2023-02-01.

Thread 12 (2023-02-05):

Can this project be used to control the A axis of grbl.

CHTUZKI, 2023-02-05:
I want to control my A-axis with this project, I don't know if it is possible with this project. If not, is it feasible for me to treat the X-axis signal as the A-axis signal. In grbl, are the six axes (XYZABC) implemented with the same code?

terjeio, 2023-02-06:
> I want to control my A-axis with this project, I don't know if it is possible with this project.

With code changes, yes.

> If not, is it feasible for me to treat the X-axis signal as the A-axis signal.

Same as above.

> In grbl, are the six axes (XYZABC) implemented with the same code?

I am not sure what you mean by this. Additional axes (to XYZ) are implemented by extending data structures and replicating code for each. The replicated code is slightly changed to reference the new axis information. This project does the same, [here are some examples](https://github.com/terjeio/GRBL_MPG_DRO_BoosterPack/blob/56ae4170ad446d3c09dc4300b88698503fb00c35/Firmware/RP2040/src/grblcomm.c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).

CHTUZKI, 2023-02-06:
Thank you for your answer

Closed 2023-02-06.

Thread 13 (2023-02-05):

"GRBL_MPG_DRO_BoosterPack" project compilation error

CHTUZKI, 2023-02-05:
I download the project from this link。`https://github.com/terjeio/GRBL_MPG_DRO_BoosterPack.git`

I use "Code Composer Studio 12.0.0" to open the `GRBL_MPG_DRO_BoosterPack-master\Firmware\TM4C123` project。I compile and the compiler tells me there are 16 errors。
`"../src/canvas/sdcard.c", line 177: error #256: type name is not allowed`
`"../src/canvas/sdcard.c", line 177: error #66: expected a ";"`
`"../src/canvas/sdcard.c", line 177: error #20: identifier "i" is undefined`
`3 errors detected in the compilation of "../src/canvas/sdcard.c".`
`gmake: *** [src/canvas/sdcard.obj] Error 1`

I made a modification to the code：

`if(!canvasSDCard) `
`{`
`       canvasSDCard = UILibCanvasCreate(0, 0, 320, 240, handlerCanvas);`
`		listPrograms = UILibListCreate((Widget *)canvasSDCard, 10, 40, 300, LISTELEMENTS, handlerProgramList);`
`		{`
`		uint_fast8_t i;`
`		for(i = 0; i < LISTELEMENTS; i++)`
`			UILibListCreateElement(listPrograms, i, "", handlerSelectList);`
`		}`
`}`

error disappears。

After I solved all the errors of this type, a new error appeared

`"./src/canvas/grblutils.obj" "./src/canvas/menu.obj" "./src/canvas/sdcard.obj" "./src/canvas/sender.obj"` `"./src/canvas/threading.obj" "./src/fonts.obj" "./src/grblcomm.obj" "./src/interface.obj" "./src/keypad.obj" "./src/main.obj"` `"../tm4c123gh6pm.cmd"  -llibc.a -l"C:/ti/TivaWare_C_Series-2.2.0.295/driverlib/ccs/Debug/driverlib.lib" `
`<Linking>`

 `undefined       first referenced  `
`  symbol                  in file       `
` ---------       ----------------  `
` serial_RxCancel ./src/grblcomm.obj`

`error #10234-D: unresolved symbols remain`
`error #10010: errors encountered during linking; "GRBL MPG and DRO Panel.out" not built`

`>> Compilation failure`
`makefile:181: recipe for target 'GRBL MPG and DRO Panel.out' failed`
`gmake: *** [GRBL MPG and DRO Panel.out] Error 1`
`gmake: Target 'all' not remade because of errors.`

`**** Build Finished ****`

CHTUZKI, 2023-02-06:
I made a modification to the code：
`__attribute__((weak)) void serial_RxCancel (void){};`

terjeio, 2023-02-06:
Retested with Tiva C after RP2040 (Pi Pico) changes, seems ok now.

Closed 2023-02-06.

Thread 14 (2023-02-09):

digression

CHTUZKI, 2023-02-09:
Sorry to take up some of your time.

I see whole project code that is event driven, like the "Display drivers" repository.
I also want to write code in an event-driven way, is there any learning material you can recommend? Or learn the route.😁😁

Thanks~

terjeio, 2023-02-13:
There are plenty of learning material available if you google for it - I learned how to do it long ago, before much learning material was available.

Closed 2023-02-11.

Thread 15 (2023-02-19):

How to use the keyboard in the "GRBL_MPG_DRO_BoosterPack" project

CHTUZKI, 2023-02-19:
Hi.

I want to use the keyboard, but I have encountered some problems. I use MSP430G2554 to drive the keyboard. The IIC interface of MSP430G2554 (keyboard board) is connected to tiva-c (DRO board), but the keyboard does not seem to work, and MPG cannot be used.

I don't know where to check. I looked at the code. The keyboard seems to be related to the UI. Can you give me some help?

Thank you.

terjeio, 2023-02-19:
Assuming you have buttons for jogging the first thing to check is the keypad strobe signal (PC4), is it going low while pressing a jog button?
Second thing is to check if the I2C bus is not stuck - both SDA (PA7) and SCL (PA6) should be 3.3V.
Do you have access to an oscilloscope or a logic analyzer?

CHTUZKI, 2023-02-20:
Thank you for your reply.

I have many questions about the keyboard processing of the "GRBL_MPG_DRO_BoosterPack" project. I am not very clear about this process
I found that MSP430G2554 is connected to the keyboard and communicates with tiva-c board through IIC, but MSP430G2554 is an IIC slave. If there is a key pressed, how can tiva-c know if there is a key pressed in time.

I found the following lines of code in the "GRBL_MPG_DRO_BoosterPack-master\Firmware\TM4C123\driver. h" file:

```
#define KEYINTR_PIN               GPIO_PIN_4  
#define KEYINTR_PORT            GPIO_PORTC_BASE
```
What is this for？

I found a function in the "GRBL_MPG_DRO_BoosterPack-master\Firmware\TM4C123\i2c. c" file:

```
void i2c_nb_send (uint32_t i2cAddr, const uint8_t value)
{
    while(i2cIsBusy);

    i2c_m.buffer[0] = value;
    i2c_m.count     = 1;
    i2c_m.data      = i2c_m.buffer;
    i2c_m.state     = I2CState_AwaitCompletion;

    I2CMasterSlaveAddrSet(I2C1_BASE, i2cAddr, false);
    I2CMasterDataPut(I2C1_BASE, *i2c_m.data);
    I2CMasterControl(I2C1_BASE, I2C_MASTER_CMD_SINGLE_SEND);
}
```
I search for this function throughout the project. I found only two calls，

`leds_setState` and `keypad_setLeds`,

They just seem to get the status of LED, where to use `i2c_nb_send` function gets the keyboard data？
Can you give me some help? Thank you very much。

terjeio, 2023-02-20:
> where to use i2c_nb_send() function gets the keyboard data？

Data is read from the MSP430 in an [interrupt handler](https://github.com/terjeio/GRBL_MPG_DRO_BoosterPack/blob/f7d28290e91c365e3bd257cd5309562a7feeda15/Firmware/TM4C123/driver.c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), the interrupt is triggered by the MSP430 pulling PC4 low. For most pins this is vith a short pulse, but for jogging the pin is held low until the key is released (key up event). When released the jog is terminated.

CHTUZKI, 2023-02-22:
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

CHTUZKI, 2023-02-22:
I'm sorry. I accidentally turned off this issue.

I'm trying. But there are still problems.

I use MSP430G2554 to drive the keyboard, and I use "Code Composer Studio 12.0.0" to debug. It seems that everything is normal, but the I2C interrupt of MSP430G2554 will never enter. I have connected the pull-up resistance on P1.6 and P1.7, which is the data displayed by my logic analyzer.

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

CHTUZKI, 2023-02-22:
yes. When P2.5 is low level, tivaC will actively request data from MSP430G2554. At this time, MSP430G2554 should enter the iic interrupt, but it did not enter. I plan to migrate MSP430G2554 code to STM32.

CHTUZKI, 2023-02-23:
Whether the "GRBL_MPG_DRO_BoosterPack" project can independently control grblHAL? I want to make an offline controller to control the grblHAL board without using the "IOsender" software. Can this project be achieved

terjeio, 2023-02-23:
Can you zip your MSP430 binary and add it to a comment so I can test it here?

> Whether the "GRBL_MPG_DRO_BoosterPack" project can independently control grblHAL?

Yes, but it will need the gcode to be stored on a SD card in the controller as the MPG do not have a local SD card.
Without a SD card manual control is possible and was the reason for why I made it in the first place.

I'll look at updating the Pico version to support a local SD card - and also add support for Pico W to allow wifi access to the card via ftp or WebDav.

CHTUZKI, 2023-02-23:
Certainly. Thank you very much for your help.

There are some Chinese code comments in it, because I want to understand the running process of the code so that I can migrate to STM32. But it's still difficult for me, because I don't know what kind of data the program outputs. I hope code comments won't cause you trouble.
[KeypadProcessor.zip](https://github.com/terjeio/GRBL_MPG_DRO_BoosterPack/files/10811076/KeypadProcessor.zip)

terjeio, 2023-02-23:
> I don't know what kind of data the program outputs

It outputs a single character based on the key pressed - or rather makes it available for reading via I2C. There are several mapping tables - from keypad scan codes to the character they represents. [This is the default map](https://github.com/terjeio/GRBL_MPG_DRO_BoosterPack/blob/f7d28290e91c365e3bd257cd5309562a7feeda15/Firmware/Keypad%20processor/main.c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).

CHTUZKI, 2023-02-23:
I tried to use arduino to simulate MSP430G2553. I manually triggered the `KEYINTR_PIN` pin of Tiva-C to let the arduino slave send a character, such as "U" and "F", but Tiva-C did not respond. I debug TivaC and found that TivaC could not trigger the `EVENT_KEYDOWN` event.

terjeio, 2023-02-23:
I have tested your version with the Launchpad connected directly to a STM32F446 grbrHAL controller with the keypad plugin enabled and it works, at least for the one button I tested - flood coolant toggle. This with a 2553 in the LaunchPad and a switch between P1.2 and P2.2. Are you testing with the LaunchPad connected to the Tiva?

> Did arduino send the wrong data,The program will use cnc_ map_ Default() function。

I cannot answer that - I do not have your Arduino code. And triggering the interrupt pin manually with a switch might be problematic due to switch bounce.

The logic analyzer trace above - was that triggered by a keypress? If so the Tiva attempted a read from they keypad processor but failed - could be due to incorrect wiring?

CHTUZKI, 2023-02-23:
Yes, I also suspect that there is a problem with my I2C connection. The picture of logic analyzer is triggered by cable short circuit. I use a wire to short P1.2 and P2.2,

CHTUZKI, 2023-02-23:
I will continue to test, thank you for your help

terjeio, 2023-02-23:
> I use 10K resistor as I2C pull-up resistor

Perhaps reduce that to 4K7 or 2K2. Anyway - the MSP430 should respond to a read request regardless of any key beeing pressed. [0 is returned if not](https://github.com/terjeio/GRBL_MPG_DRO_BoosterPack/blob/f7d28290e91c365e3bd257cd5309562a7feeda15/Firmware/Keypad%20processor/main.c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). Or your MSP430 has blown pins?

CHTUZKI, 2023-02-23:
I re-ordered an MSP430G2553 from the Internet. I feel that there may be a problem with my chip. When the chip is mailed to me, I will continue to test it.

terjeio, 2023-02-24:
One thing to be aware of with the MPS430 LaunchPad is that P1.6 is connected to user LED2 via a jumper. IIRC this may interfere with I2C operation so perhaps it is good practice to remove the jumper? BTW it worked for me with the jumper in place but then I have pull-up resistors with a lower value than you have.

CHTUZKI, 2023-02-25:
There is no problem with the keyboard. happy. It's just a small problem. My I2C resistance may be too large. After I replace the resistance of 10K with the resistance of 4K7, the problem is solved.

It seems that my knowledge of hardware is still lacking😂

Thank you for your long help。

Closed 2023-02-22.

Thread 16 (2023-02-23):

MPG cannot be used

CHTUZKI, 2023-02-23:
Can the "GRBL_MPG_DRO_BoosterPack" project use MPG when the keyboard is unavailable?

My MPG is connected to the PC5 and PC6 pins of TivaC. When I rotate the MPG, nothing happens.

I connected a switch at the `MPG_MODE_PIN` pin and put the program in MPG mode. The X-axis label on the TFT screen also turned green.

CHTUZKI, 2023-02-23:
In the TM4C123/driver. c file:
```
static void MPG_X_IntHandler (void)
{
    uint32_t pos;
    static int32_t last = 0;

    QEIIntClear(QEI0_BASE, QEI_INTTIMER);

    if((pos = QEIPositionGet(QEI0_BASE)) != last)
    {
        last = pos;
        mpg.x.position = ((int32_t)pos - MID_POS);
        mpg.x.velocity = QEIVelocityGet(QEI0_BASE);
        if(interface.on_mpgChanged)
        {
            interface.on_mpgChanged(mpg);
        }
    }
}
```
`interface.on_mpgChanged(mpg);`It will not be executed. I found that the function pointer will be cleared after the program enters the main interface.

In the file dro. c:
```
        case EventWidgetPainted:;
            uint_fast8_t i;
            char rpm[10];
            event = 0;
            isReady = false;
            setBackgroundColor(canvasMain->widget.bgColor);
            grbl_data = setGrblReceiveCallback(displayGrblData);
            for(i = 0; i < 3; i++) {
                if(axis[i].visible) {
                    axis[i].lblAxis->widget.fgColor = i == mpg_axis ? Green : White;
                    UILibLabelDisplay(axis[i].lblAxis, axis[i].label);
#ifdef LATHEMODE
                    if(i == X_AXIS)
                        displayXMode("?");
#endif
                }
            }
            drawString(font_freepixel_17x34, 5, RPMROW, "RPM:", false);
            sprintf(rpm, "%6.1f", mpg_rpm);
            lblRPM->widget.fgColor = Coral;
            UILibLabelDisplay(lblRPM, rpm);
            drawString(font_23x16, 220, RPMROW - 3, "Jog:", false);
            drawString(font_23x16, 87, STATUSROW, "Feed:", true);
            setJogModeChangedCallback(jogModeChanged);
            if(grbl_data->mpgMode) {
                displayMPGFactor(X_AXIS, axis[X_AXIS].mpg_idx);
                displayMPGFactor(Y_AXIS, axis[Y_AXIS].mpg_idx);
                displayMPGFactor(Z_AXIS, axis[Z_AXIS].mpg_idx);
            }
            mpgReset = true;
            leds = leds_getState();
            keypad_forward(!grbl_data->mpgMode);
            setKeyclickCallback2(keyEvent, false);
            NavigatorSetPosition(0, nav_midpos, false);
//            serial_putC(CMD_STATUS_REPORT_ALL); // Request realtime status from grbl
            active = true;
            break;
```

`setKeyclickCallback2(keyEvent, false);`Will clear `interface.on_ MpgChanged` function pointer.

terjeio, 2023-02-24:
> Can the "GRBL_MPG_DRO_BoosterPack" project use MPG when the keyboard is unavailable?

Not without modifying code or ensuring that the code starts with MPG mode on.

> My MPG is connected to the PC5 and PC6 pins of TivaC. When I rotate the MPG, nothing happens.

In DRO mode the MPG [encoders are polled](https://github.com/terjeio/GRBL_MPG_DRO_BoosterPack/blob/f7d28290e91c365e3bd257cd5309562a7feeda15/Firmware/TM4C123/src/canvas/dro.c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) and the callback is set to NULL. Polling is only done when connected to a controller and [MPG mode](https://github.com/terjeio/GRBL_MPG_DRO_BoosterPack#mpg-microcontroller) has been accepted by it. MPG mode might be entered automatically on startup or requested by pulling the MPG mode pin low. The controller will respond with a `|MPG:1` element in the real-time report if accepted. The request is made when a keypress (0x0D - carriage return) is received from the keypad controller.
The MPG callback is only used in some of the data entry canvases to adjust values.

> I connected a switch at the MPG_MODE_PIN pin and put the program in MPG mode.

Is the MPG connected to a controller that has MPG mode enabled? And is the MPG mode request accepted?
FYI [ioSender](https://github.com/terjeio/ioSender) greys out the UI if MPG mode is active.

CHTUZKI, 2023-02-24:
Powerful projects, I will continue to explore

Closed 2023-02-27.

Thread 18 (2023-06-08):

About the issue of sending G-code with GRBL_MPG_DRO

CHTUZKI, 2023-06-08:
HI.
I am trying the GRBL_MPG_DRO project and using a TIVA-C board. I have some questions about the logic of sending G-code from the TIVA-C board. Can I use the grblSendSerial() function in a while loop to continuously send G-code from the TIVA-C board? Will grblHAL lose G-code if the TIVA-C board sends too fast? I noticed that iosender sends G-code line by line to grblHAL, and grblHAL returns an OK to iosender after receiving each line of G-code. I am curious if there is a delay between each line of G-code sent by iosender, which may cause grblHAL to run smoothly or not. Does grblHAL have a buffer that can store multiple lines of G-code at once to avoid delays between each line of G-code?

best regards.

terjeio, 2023-06-08:
>  Can I use the grblSendSerial() function in a while loop to continuously send G-code

Yes and no. You have to wait for the "ok" response before sending the next line. Or use the character counting method to ensure that the controller buffer does not overflow.

There is a [sender canvas](https://github.com/terjeio/GRBL_MPG_DRO_BoosterPack/blob/master/Firmware/TM4C123/src/canvas/sender.c) that you can use for transmission, this takes a pointer to a function that delivers the next line of gcode to the sender. The sender will call this function to get the next line (block) when it is safe to send it.
IIRC the sender handles feed hold, abort etc.

> Does grblHAL have a buffer that can store multiple lines of G-code at once to avoid delays between each line of G-code?

Yes, most grblHAL controllers has a 1Kbyte buffer. The size is available in the `$I` response. The `Bf:` element in the realtime report contains number of free characters in the buffer.

Closed 2023-06-09.

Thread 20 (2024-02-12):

Pi Pico Board, LED resistor calculation?

Overlights, 2024-02-12:
Hello Terje,
Sorry to bother you.
I made some layout changes to your MPG DRO board, to make it a little more versatile (in my opinion), but the circuit is the same.
Among the various small modifications (I'll tell you about them in detail in another context), I added a double Pad to the LED resistors.
In this way, the predefined SMD resistors (on bottom) can be easily replaced with Custom resistors on Top
(1/4W, standard tht), simply cutting the track of the corresponding SMD resistor (the precise point is indicated on Bottom).

Finally, the calculation is needed for the correct resistance value, for a given LED Vf (based on the color chosen) and for a given current (say 10mA, as an average value).

I imagined it was:
R(led) = (Vcc - Vf) / Iled

So giving two examples:
(5 - 1.8) / 0.010 = 320 ohm (red LED, Vf=1.8V)
(5 - 3.6) / 0.010 = 140 ohm (white/blue LED, Vf=3.6V)

But in this post:
https://github.com/terjeio/GRBL_MPG_DRO_BoosterPack/issues/3#issuecomment-1011856945
you said you used 2.7K resistors for standard 3 mm LEDs, obtaining different light intensities, I suppose depending on the color of the LEDs.

If the formula above was correct, with a res. from 2.7K, I would get about 1 mA for a red LED, 0.5 mA for a white one.
Something doesn't add up.
Where am I doing wrong?

Regards,
Marco

carneeki, 2024-02-12:
Maybe it's meant to be 270 ohms? We can swap the resistance and I_led in
the equation to get I_led:

(5-1.8) / 270 = 0.012 = 12ma
(5-3.6) / 270 = 0.005 = 5ma

and don't seem unreasonable values, though 5ma might be too dim for some
use cases.

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

--
Adam "carneeki" Carmichael
p: 0435 908 000
w: http://carneeki.github.io
e: ***@***.***
i: 2207644

Overlights, 2024-02-12:
Hi Adam,
Exactly.
12 mA would be an absolutely reasonable value, while 5 mA, a bit low.
Having to choose a conservative standard value (for pre-soldered SMD resistors), it would be the one for an average LED current of 10 - 15 mA, for the lowest Vf value (red LED, approximately 1.8V).
So:
(5 - 1.8) / 0.010 = 320 ohms
(5 - 1.8) / 0.015 = 213 ohms
Or as you were saying, 270 ohms, for 12 mA.
All LEDs with higher Vf will have a proportionally lower brightness.

carneeki, 2024-02-12:
Hi Marco,

I'm assuming you're wanting to optimise either the number of resistors you
keep on the shelf (or maybe how many reels a pick'n'place machine will need
loaded). To that end, I'd suggest using the same value resistor either in
series or parallel, and the E24 resistor values are really well optimised
for both cases -

For red (1.8V):
(5-1.8) / 300 = 10.7mA

For white / blue (3.6V), 2x 300 in parallel:
(5-3.6) / 150 = 9.3mA

This comes at the compromise of needing to use more components, but they're
the same value. It also permits (with a solder jumper and the parallel
pair) the option to have this as something the end user can choose if they
are plugging LEDs into a header.

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

--
Adam "carneeki" Carmichael
p: 0435 908 000
w: http://carneeki.github.io
e: ***@***.***
i: 2207644

Overlights, 2024-02-12:
No Adam,
I'm not going to change the default value of the SMD LED resistors, just make sure it was correct.
I guess Terje can clarify this.

As written above, I modified the layout of the Board with a double SMD - THT pad, for all the LED resistors.
The SMD resistors will all have the same value, suitable for the worst condition described above (for example, 220 ohm, for a red LED with a Vf of 1.8V for approximately 15 mA, or 270 ohm for approximately 12 mA)
But anyone will be able to implement LEDs of other colors, therefore with a specific Vf, replacing the default SMD resistor with a 1/4W THT resistor of the most suitable value.

terjeio, 2024-02-12:
Not easy this as modern LEDs seems to vary quite a bit in brightness depending on the color and perhaps the manufacturer as well?. E.g. a test board I made with SMD LEDs uses resistors ranging from 680E to 4K7. So having the option of adding a second resistor is IMO a good idea.

Overlights, 2024-02-14:
Thank you Terje,
I mainly wanted to make sure that the calculation for the LED resistors was correct, so that I could choose a standard value for all SMD resistors.
As described above, I would use 270 ohm, a suitable value for a standard Red LED (3 or 5 mm.). So a Vf of around 1.8V for 12 mA.
LEDs with different characteristics can still be implemented, using the second THT Pad for custom resistors.

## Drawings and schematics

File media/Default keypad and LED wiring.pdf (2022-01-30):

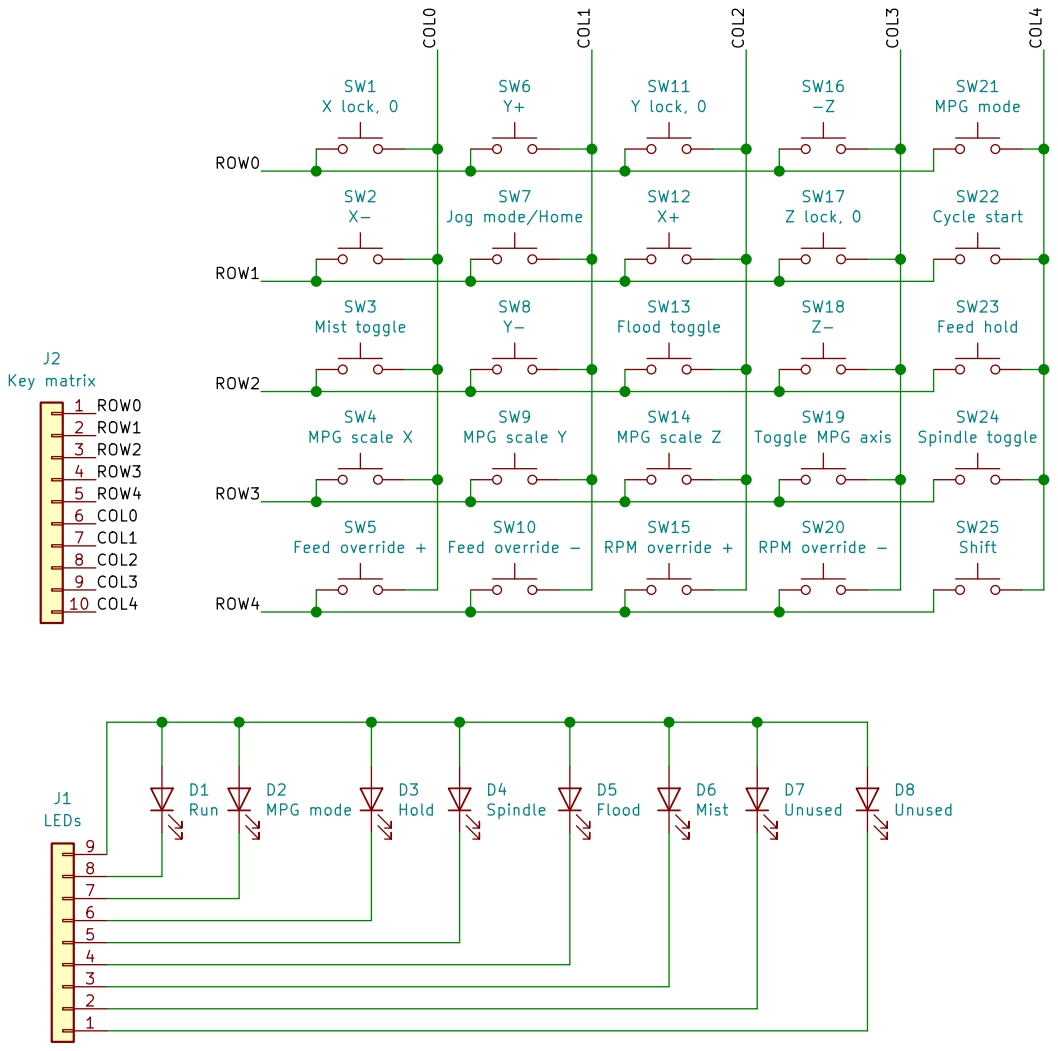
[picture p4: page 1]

Jog mode/Home SW8 Y- SW9 MPG scale Y

Io Engineering / Terje Io
File: 5x5 keypad.sch Sheet: /
Id: 1/1 Title: MPG & DRO Keypad & LED default assignments

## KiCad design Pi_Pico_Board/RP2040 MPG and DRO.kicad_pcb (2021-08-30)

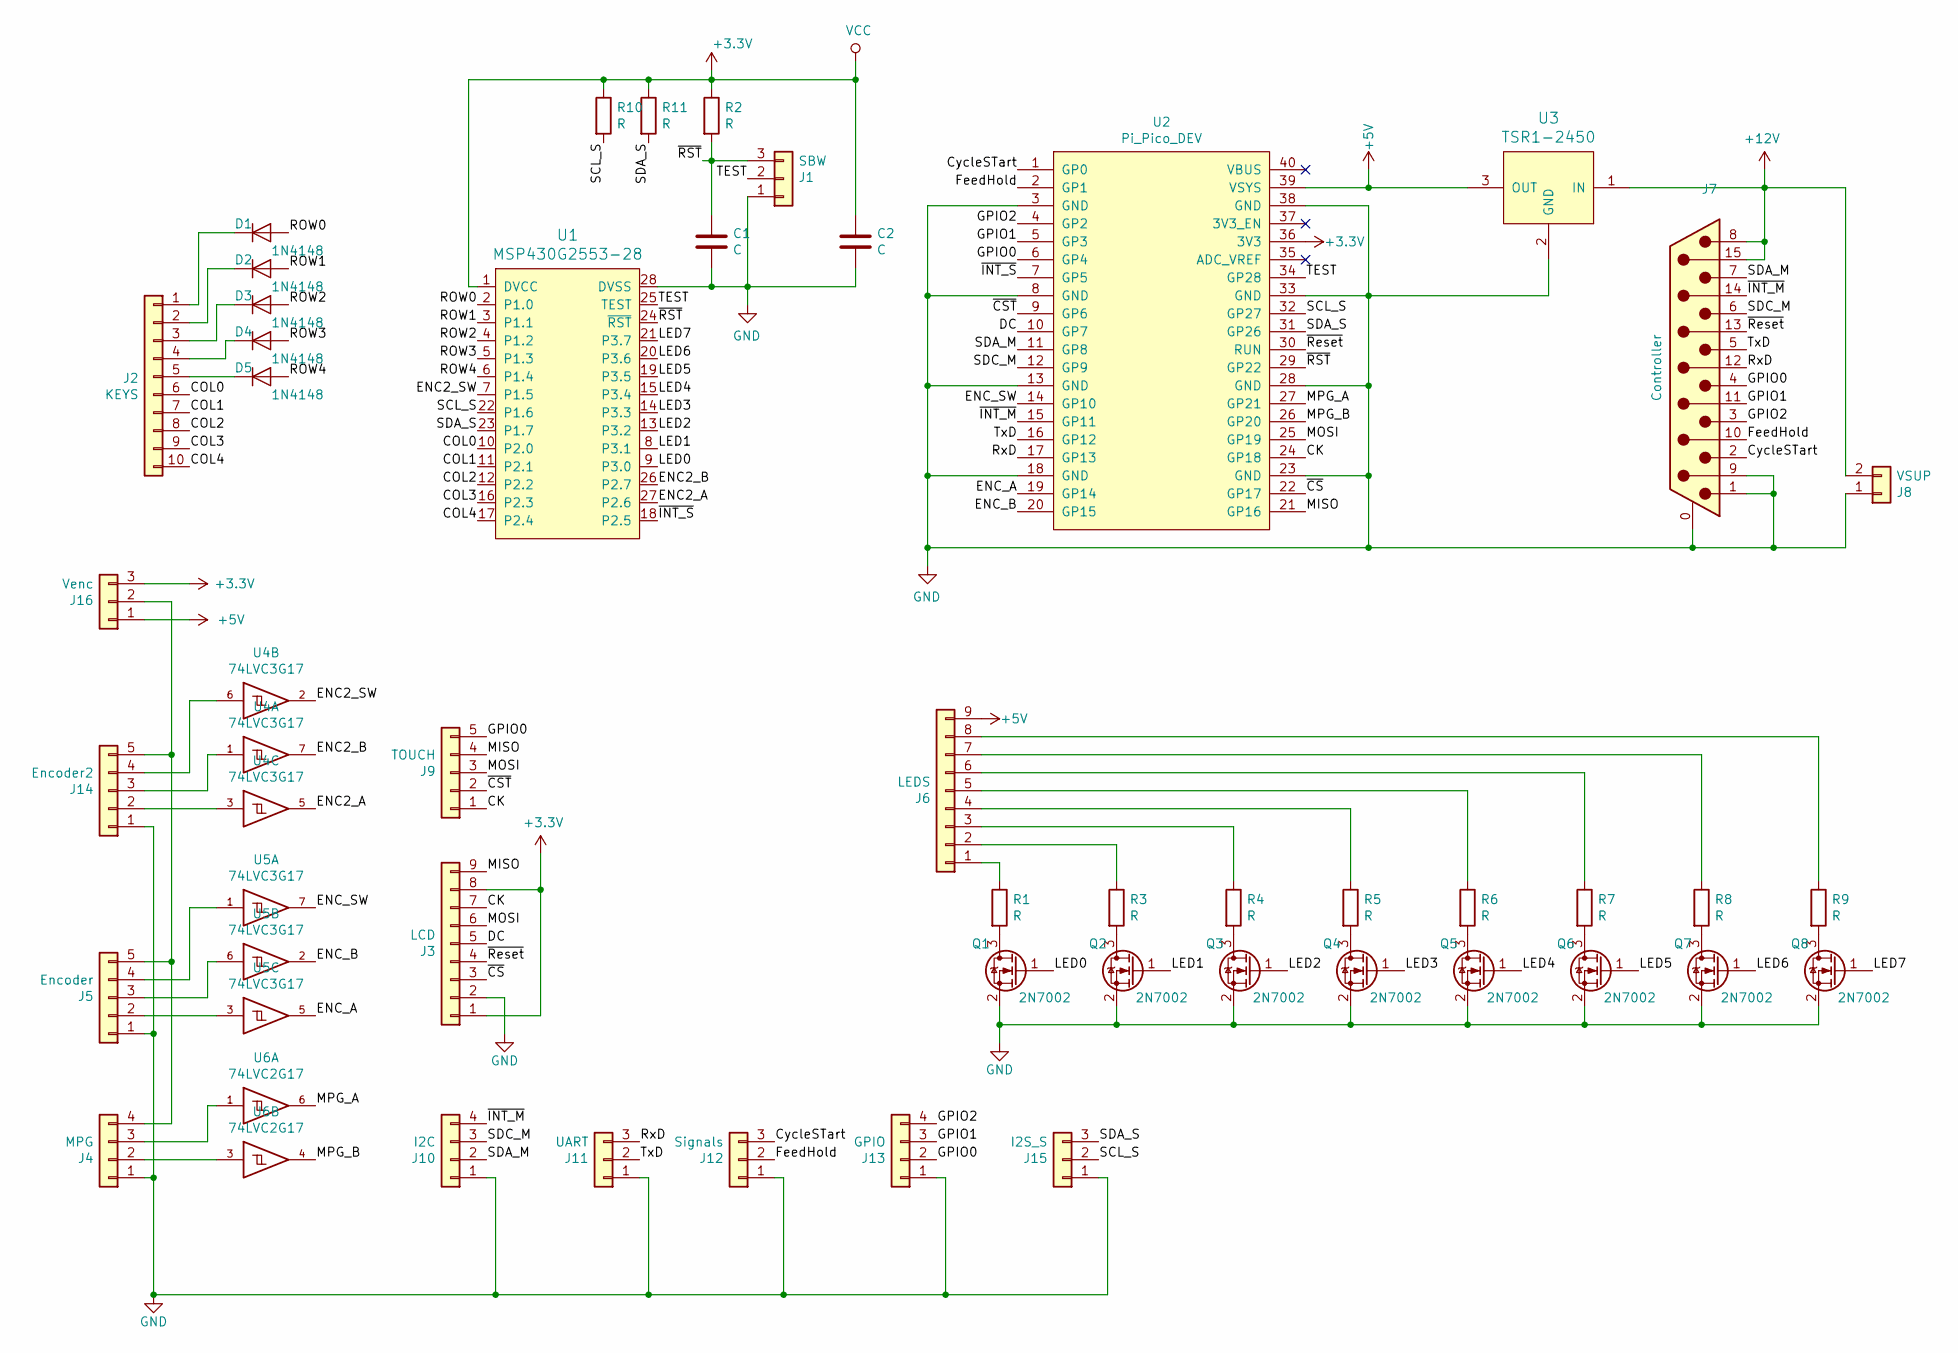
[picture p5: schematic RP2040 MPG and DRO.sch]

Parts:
C1, C2: C; C_0805_2012Metric
D1, D2, D3, D4, D5: 1N4148; D_SOD-123
J1: SBW; PinHeader_1x03_P2.54mm_Vertical
J2: KEYS; PinHeader_1x10_P2.54mm_Vertical
J3: LCD; PinHeader_1x09_P2.54mm_Vertical
J4: MPG; PinHeader_1x04_P2.54mm_Vertical
J5: Encoder; PinHeader_1x05_P2.54mm_Vertical
J6: LEDS; PinHeader_1x09_P2.54mm_Vertical
J7: Controller; DB15
J8: VSUP; PinHeader_1x02_P2.54mm_Vertical
J9: TOUCH; PinHeader_1x05_P2.54mm_Vertical
J10: I2C; PinHeader_1x04_P2.54mm_Vertical
J11: UART; PinHeader_1x03_P2.54mm_Vertical
J12: Signals; PinHeader_1x03_P2.54mm_Vertical
J13: GPIO; PinHeader_1x04_P2.54mm_Vertical
J14: Encoder2; PinHeader_1x05_P2.54mm_Vertical
J15: I2S_S; PinHeader_1x03_P2.54mm_Vertical
J16: Venc; PinHeader_1x03_P2.54mm_Vertical
Q1, Q2, Q3, Q4, Q5, Q6, Q7, Q8: 2N7002; SOT-23
R1, R2, R3, R4, R5, R6, R7, R8, R9, R10, R11: R; R_0805_2012Metric
U1: MSP430G2553-28; TSSOP-28_4.4x9.7mm_P0.65mm
U2: Pi_Pico_DEV
U3: TSR1-2450; TSR_1
U4, U5: 74LVC3G17; SSOP-8_2.95x2.8mm_P0.65mm
U6: 74LVC2G17; SOT-23-6

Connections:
+3V3: C2.1, J3.1, J3.8, J16.3, R2.1, R10.1, R11.1, U1.1 (DVCC), U2.36 (3V3), U4.8 (VCC), U5.8 (VCC), U6.5 (VCC)
+5V: J6.9, J16.1, U2.39 (VSYS), U3.3 (OUT)
+12V: J7.8, J7.15, J8.2, U3.1 (IN)
/CK: J3.7, J9.1, U2.24 (GP18)
/COL0: J2.6, U1.10 (P2.0)
/COL1: J2.7, U1.11 (P2.1)
/COL2: J2.8, U1.12 (P2.2)
/COL3: J2.9, U1.16 (P2.3)
/COL4: J2.10, U1.17 (P2.4)
/CycleSTart: J7.2, J12.3, U2.1 (GP0)
/DC: J3.5, U2.10 (GP7)
/ENC2_A: U1.27 (P2.6), U4.5
/ENC2_B: U1.26 (P2.7), U4.7
/ENC2_SW: U1.7 (P1.5), U4.2
/ENC_A: U2.19 (GP14), U5.5
/ENC_B: U2.20 (GP15), U5.2
/ENC_SW: U2.14 (GP10), U5.7
/FeedHold: J7.10, J12.2, U2.2 (GP1)
/GPIO0: J7.4, J9.5, J13.2, U2.6 (GP4)
/GPIO1: J7.11 (P111), J13.3, U2.5 (GP3)
/GPIO2: J7.3, J13.4, U2.4 (GP2)
/LED0: Q1.1 (G), U1.9 (P3.0)
/LED1: Q2.1 (G), U1.8 (P3.1)
/LED2: Q3.1 (G), U1.13 (P3.2)
/LED3: Q4.1 (G), U1.14 (P3.3)
/LED4: Q5.1 (G), U1.15 (P3.4)
/LED5: Q6.1 (G), U1.19 (P3.5)
/LED6: Q7.1 (G), U1.20 (P3.6)
/LED7: Q8.1 (G), U1.21 (P3.7)
/MISO: J3.9, J9.4, U2.21 (GP16)
/MOSI: J3.6, J9.3, U2.25 (GP19)
/MPG_A: U2.27 (GP21), U6.6
/MPG_B: U2.26 (GP20), U6.4
/ROW0: D1.2 (A), U1.2 (P1.0)
/ROW1: D2.2 (A), U1.3 (P1.1)
/ROW2: D3.2 (A), U1.4 (P1.2)
/ROW3: D4.2 (A), U1.5 (P1.3)
/ROW4: D5.2 (A), U1.6 (P1.4)
/RxD: J7.12, J11.3, U2.17 (GP13)
/SCL_S: J15.2, R10.2, U1.22 (P1.6), U2.32 (GP27)
/SDA_M: J7.7, J10.2, U2.11 (GP8)
/SDA_S: J15.3, R11.2, U1.23 (P1.7), U2.31 (GP26)
/SDC_M: J7.6, J10.3, U2.12 (GP9)
/TEST: J1.2, U1.25 (TEST), U2.34 (GP28)
/TxD: J7.5, J11.2, U2.16 (GP12)
/~CS: J3.3, U2.22 (GP17)
/~CST: J9.2, U2.9 (GP6)
/~INT_M: J7.14, J10.4, U2.15 (GP11)
/~INT_S: U1.18 (P2.5), U2.7 (GP5)
/~RST: C1.1, J1.3, R2.2, U1.24 (~RST~), U2.29 (GP22)
/~Reset: J3.4, J7.13, U2.30 (RUN)
GND: C1.2, C2.2, J1.1, J3.2, J4.1, J5.1, J7.0 (PAD), J7.1, J7.9, J8.1, J10.1, J11.1, J12.1, J13.1, J14.1, J15.1, Q1.2 (S), Q2.2 (S), Q3.2 (S), Q4.2 (S), Q5.2 (S), Q6.2 (S), Q7.2 (S), Q8.2 (S), U1.28 (DVSS), U2.3 (GND), U2.8 (GND), U2.13 (GND), U2.18 (GND), U2.23 (GND), U2.28 (GND), U2.33 (GND), U2.38 (GND), U3.2 (GND), U4.4 (GND), U5.4 (GND), U6.2 (GND)
unnamed: D1.1 (K), J2.1
unnamed: D2.1 (K), J2.2
unnamed: D3.1 (K), J2.3
unnamed: D4.1 (K), J2.4
unnamed: D5.1 (K), J2.5
unnamed: J4.2, U6.3
unnamed: J4.3, U6.1
unnamed: J5.2, U5.3
unnamed: J5.3, U5.6
unnamed: J5.4, U5.1
unnamed: J6.1, R1.1
unnamed: J6.2, R3.1
unnamed: J6.3, R4.1
unnamed: J6.4, R5.1
unnamed: J6.5, R6.1
unnamed: J6.6, R7.1
unnamed: J6.7, R8.1
unnamed: J6.8, R9.1
unnamed: J14.2, U4.3
unnamed: J14.3, U4.1
unnamed: J14.4, U4.6
unnamed: J4.4, J5.5, J14.5, J16.2
unnamed: Q1.3 (D), R1.2
unnamed: Q2.3 (D), R3.2
unnamed: Q3.3 (D), R4.2
unnamed: Q4.3 (D), R5.2
unnamed: Q5.3 (D), R6.2
unnamed: Q6.3 (D), R7.2
unnamed: Q7.3 (D), R8.2
unnamed: Q8.3 (D), R9.2

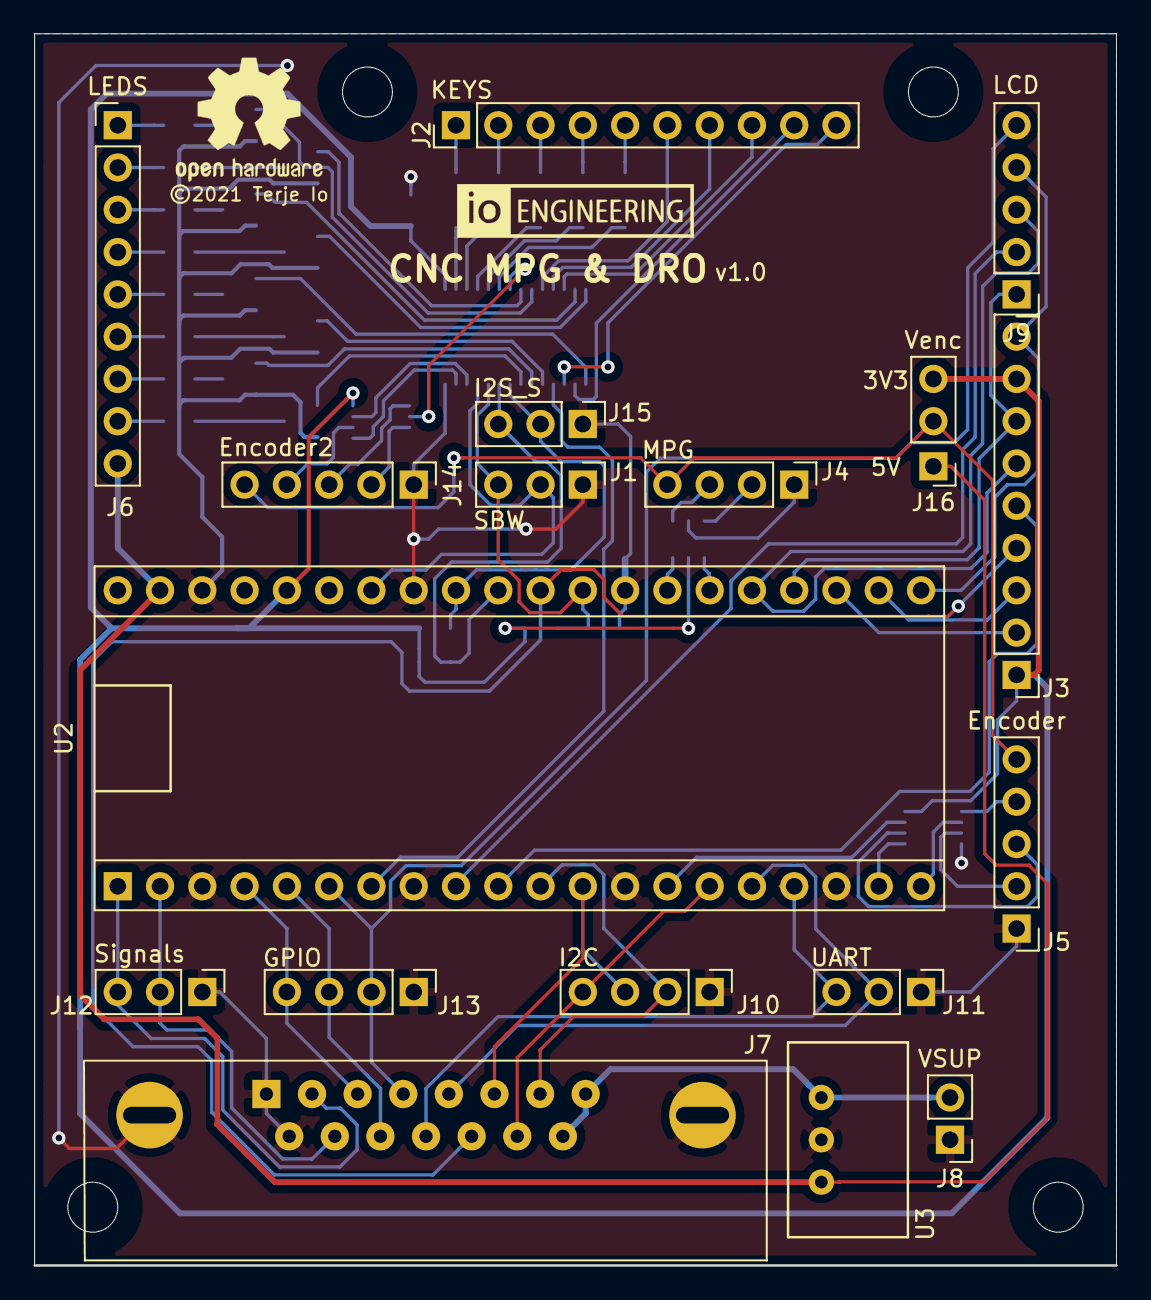
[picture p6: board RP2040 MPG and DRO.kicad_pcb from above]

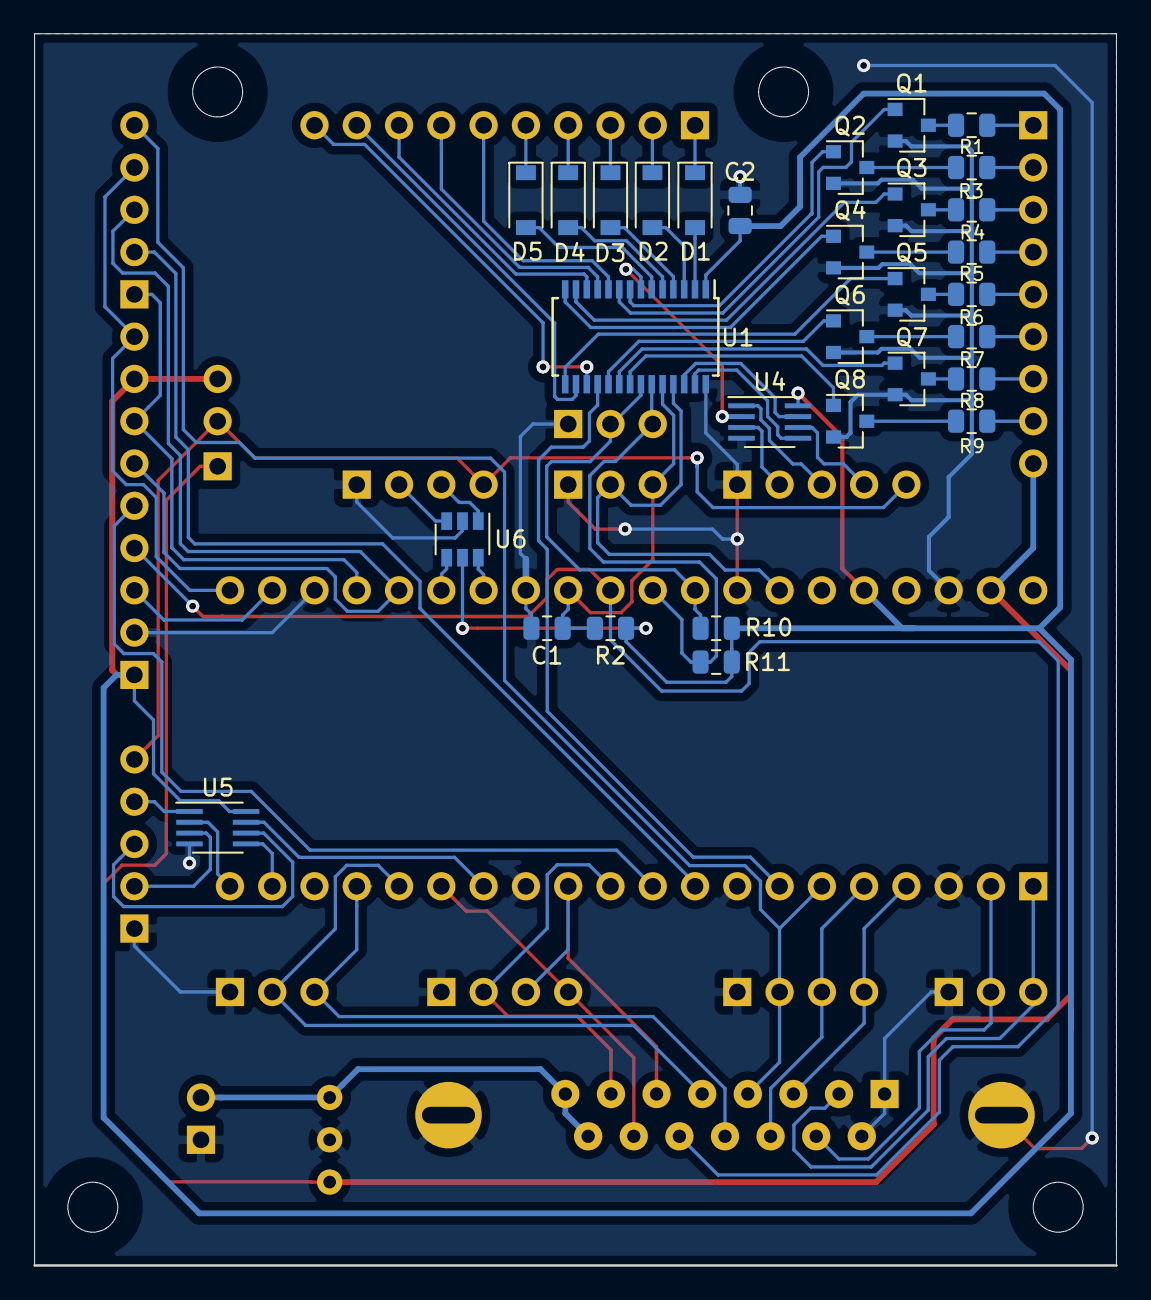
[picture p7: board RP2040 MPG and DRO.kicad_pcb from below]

Board: 2 copper layers, 65.0 x 74.0 mm, 48 parts (30 on the bottom side), 82 nets.

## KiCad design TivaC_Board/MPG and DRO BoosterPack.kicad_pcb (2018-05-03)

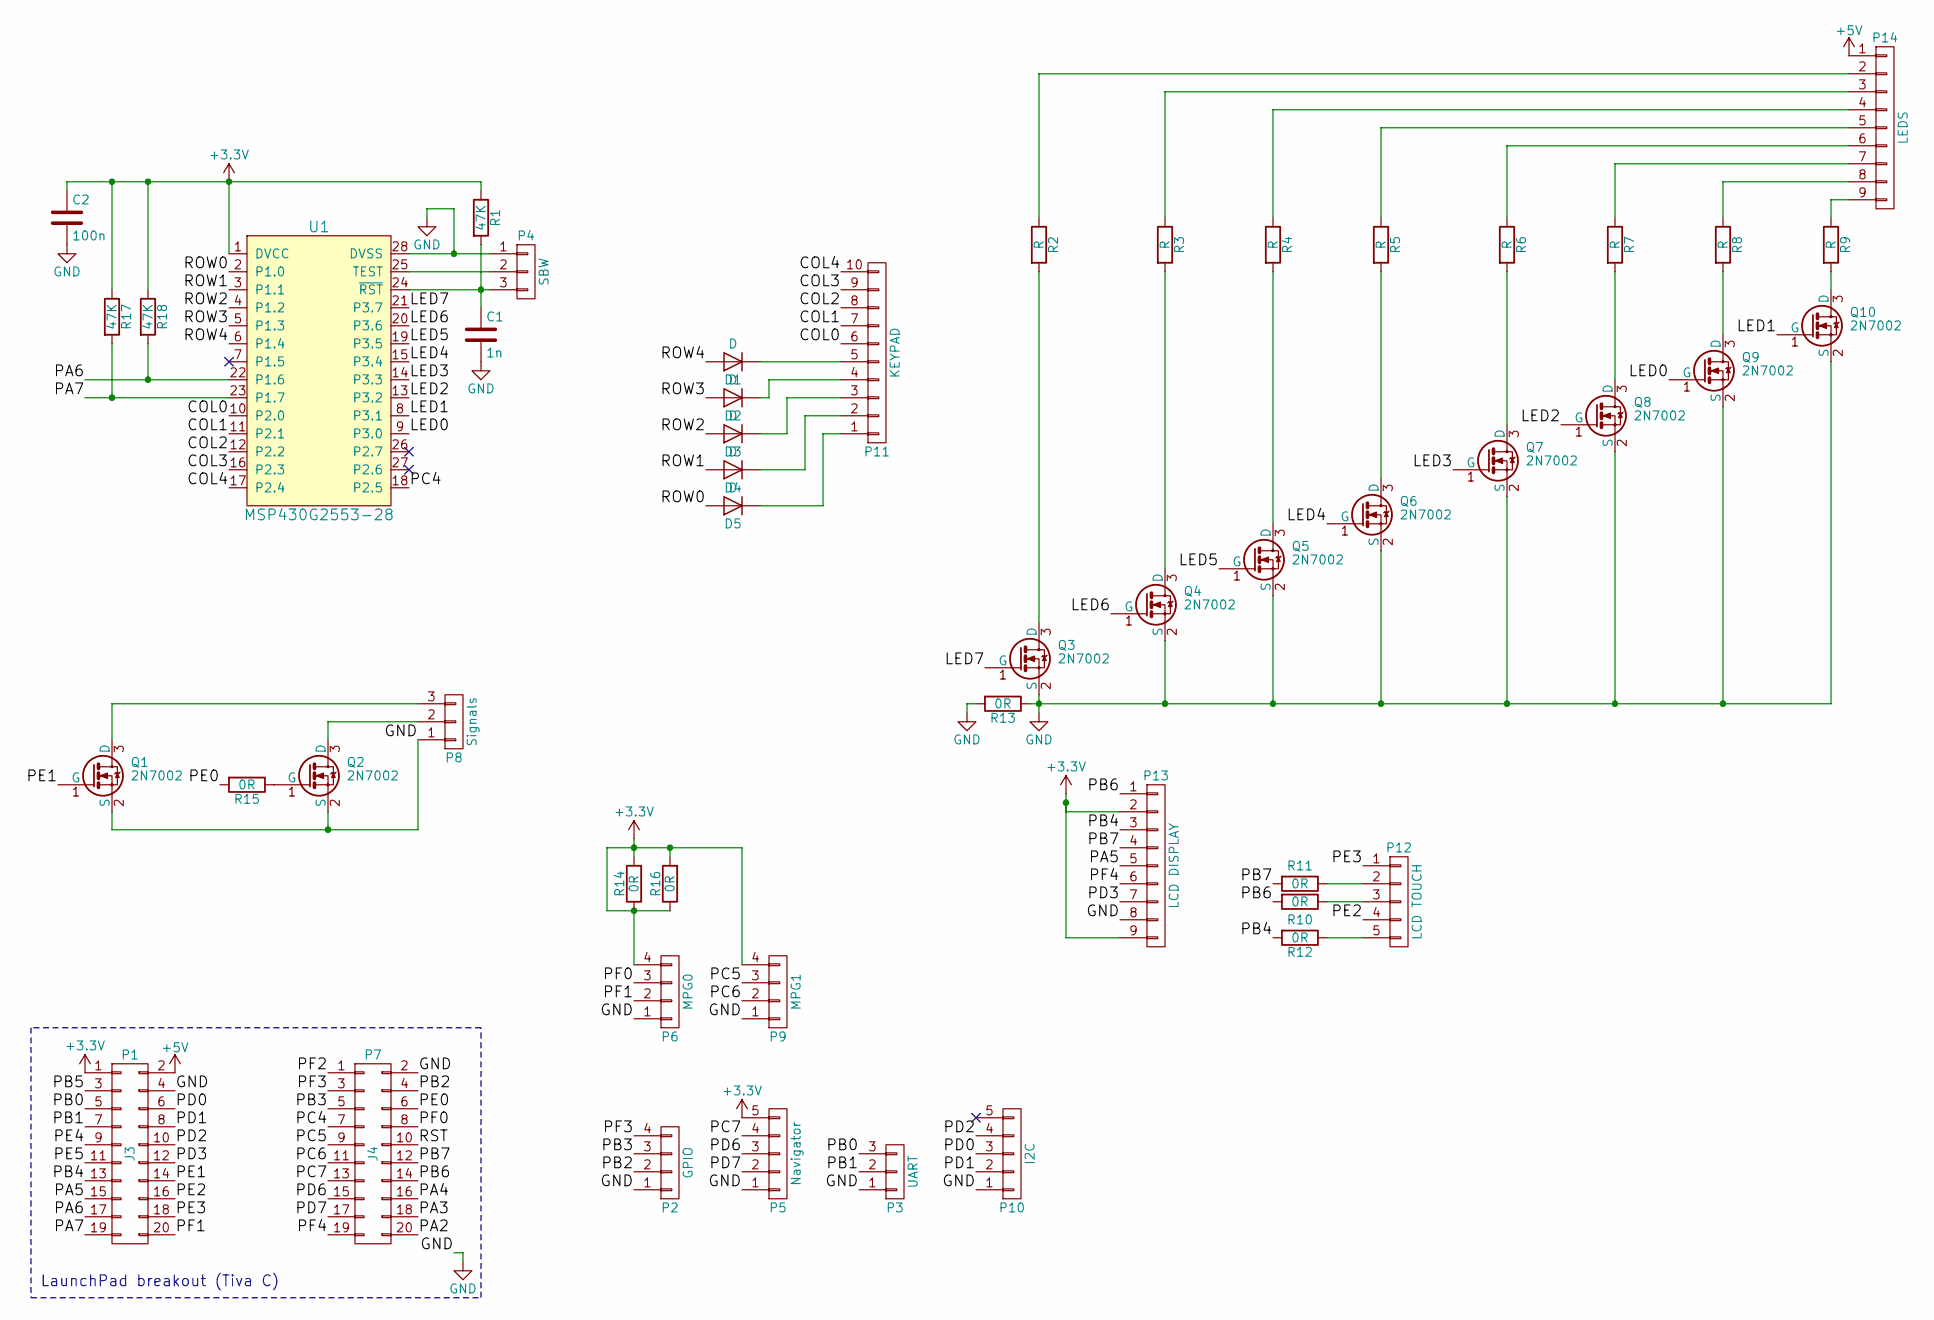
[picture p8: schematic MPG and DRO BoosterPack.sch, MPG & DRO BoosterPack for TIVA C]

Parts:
C1: 1n; C_0805
C2: 100n; C_0805
D1, D2, D3, D4, D5: D; D_SOD-123
P1: J3; Socket_Strip_Straight_2x10_SMD
P2: GPIO; Pin_Header_Straight_1x04_Pitch2.54mm
P3: UART; Pin_Header_Straight_1x03_Pitch2.54mm
P4: SBW; Pin_Header_Straight_1x03_Pitch2.54mm
P5: Navigator; Pin_Header_Straight_1x05_Pitch2.54mm
P6: MPG0; Pin_Header_Straight_1x04_Pitch2.54mm
P7: J4; Socket_Strip_Straight_2x10_SMD
P8: Signals; Pin_Header_Straight_1x03_Pitch2.54mm
P9: MPG1; Pin_Header_Straight_1x04_Pitch2.54mm
P10: I2C; Pin_Header_Straight_1x05_Pitch2.54mm
P11: KEYPAD; Pin_Header_Straight_1x10_Pitch2.54mm
P12: LCD TOUCH; Pin_Header_Straight_1x05_Pitch2.54mm
P13: LCD DISPLAY; Pin_Header_Straight_1x09_Pitch2.54mm
P14: LEDS; Pin_Header_Straight_1x09_Pitch2.54mm
Q1, Q2, Q3, Q4, Q5, Q6, Q7, Q8, Q9, Q10: 2N7002; SOT-23
R1, R17, R18: 47K; R_0805
R2, R3, R4, R5, R6, R7, R8, R9: R; R_0805
R10, R11, R12, R13, R14: 0R; R_1206
R15, R16: 0R; R_0805
U1: MSP430G2553-28; TSSOP-28_4.4x9.7mm_Pitch0.65mm

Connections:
+3V3: C2.1, P1.1, P5.5, P6.4, P9.4, P13.2, P13.9, R1.1, R14.1, R14.2, R16.1, R16.2, R17.1, R18.1, U1.1 (DVCC)
+5V: P1.2, P14.1
/COL0: P11.6, U1.10 (P2.0)
/COL1: P11.7, U1.11 (P2.1)
/COL2: P11.8, U1.12 (P2.2)
/COL3: P11.9, U1.16 (P2.3)
/COL4: P11.10, U1.17 (P2.4)
/LED0: Q9.1 (G), U1.9 (P3.0)
/LED1: Q10.1 (G), U1.8 (P3.1)
/LED2: Q8.1 (G), U1.13 (P3.2)
/LED3: Q7.1 (G), U1.14 (P3.3)
/LED4: Q6.1 (G), U1.15 (P3.4)
/LED5: Q5.1 (G), U1.19 (P3.5)
/LED6: Q4.1 (G), U1.20 (P3.6)
/LED7: Q3.1 (G), U1.21 (P3.7)
/PA2: P7.20
/PA3: P7.18
/PA4: P7.16
/PA5: P1.15, P13.5
/PA6: P1.17, R18.2, U1.22 (P1.6)
/PA7: P1.19, R17.2, U1.23 (P1.7)
/PB0: P1.5, P3.3
/PB1: P1.7, P3.2
/PB2: P2.2, P7.4
/PB3: P2.3, P7.5
/PB4: P1.13, P13.3, R12.2
/PB5: P1.3
/PB6: P7.14, P13.1, R10.2
/PB7: P7.12, P13.4, R11.2
/PC4: P7.7, U1.18 (P2.5)
/PC5: P7.9, P9.3
/PC6: P7.11, P9.2
/PC7: P5.4, P7.13
/PD0: P1.6, P10.3
/PD1: P1.8, P10.2
/PD2: P1.10, P10.4
/PD3: P1.12, P13.7
/PD6: P5.3, P7.15
/PD7: P5.2, P7.17
/PE0: P7.6, R15.2
/PE1: P1.14, Q1.1 (G)
/PE2: P1.16, P12.4
/PE3: P1.18, P12.1
/PE4: P1.9
/PE5: P1.11
/PF0: P6.3, P7.8
/PF1: P1.20, P6.2
/PF2: P7.1
/PF3: P2.4, P7.3
/PF4: P7.19, P13.6
/ROW0: D5.2 (A), U1.2 (P1.0)
/ROW1: D4.2 (A), U1.3 (P1.1)
/ROW2: D3.2 (A), U1.4 (P1.2)
/ROW3: D2.2 (A), U1.5 (P1.3)
/ROW4: D1.2 (A), U1.6 (P1.4)
/RST: P7.10
GND: C1.2, C2.2, P1.4, P2.1, P3.1, P4.1, P5.1, P6.1, P7.2, P8.1, P9.1, P10.1, P13.8, Q1.2 (S), Q2.2 (S), Q3.2 (S), Q4.2 (S), Q5.2 (S), Q6.2 (S), Q7.2 (S), Q8.2 (S), Q9.2 (S), Q10.2 (S), R13.1, R13.2, U1.28 (DVSS)
unnamed: C1.1, P4.3, R1.2, U1.24 (~RST~)
unnamed: D1.1 (K), P11.5
unnamed: D2.1 (K), P11.4
unnamed: D3.1 (K), P11.3
unnamed: D4.1 (K), P11.2
unnamed: D5.1 (K), P11.1
unnamed: P4.2, U1.25 (TEST)
unnamed: P8.2, Q2.3 (D)
unnamed: P8.3, Q1.3 (D)
unnamed: P12.2, R11.1
unnamed: P12.3, R10.1
unnamed: P12.5, R12.1
unnamed: P14.2, R2.1
unnamed: P14.3, R3.1
unnamed: P14.4, R4.1
unnamed: P14.5, R5.1
unnamed: P14.6, R6.1
unnamed: P14.7, R7.1
unnamed: P14.8, R8.1
unnamed: P14.9, R9.1
unnamed: Q2.1 (G), R15.1
unnamed: Q3.3 (D), R2.2
unnamed: Q4.3 (D), R3.2
unnamed: Q5.3 (D), R4.2
unnamed: Q6.3 (D), R5.2
unnamed: Q7.3 (D), R6.2
unnamed: Q8.3 (D), R7.2
unnamed: Q9.3 (D), R8.2
unnamed: Q10.3 (D), R9.2

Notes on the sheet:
LaunchPad breakout (Tiva C)

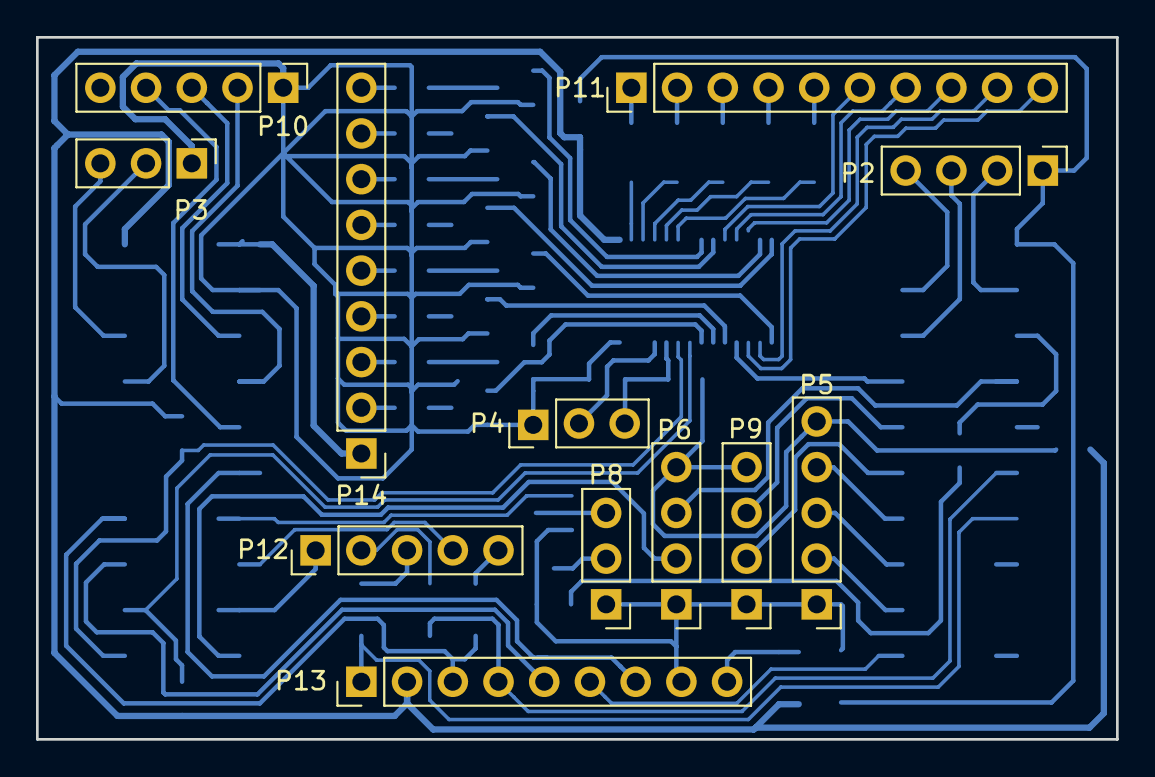
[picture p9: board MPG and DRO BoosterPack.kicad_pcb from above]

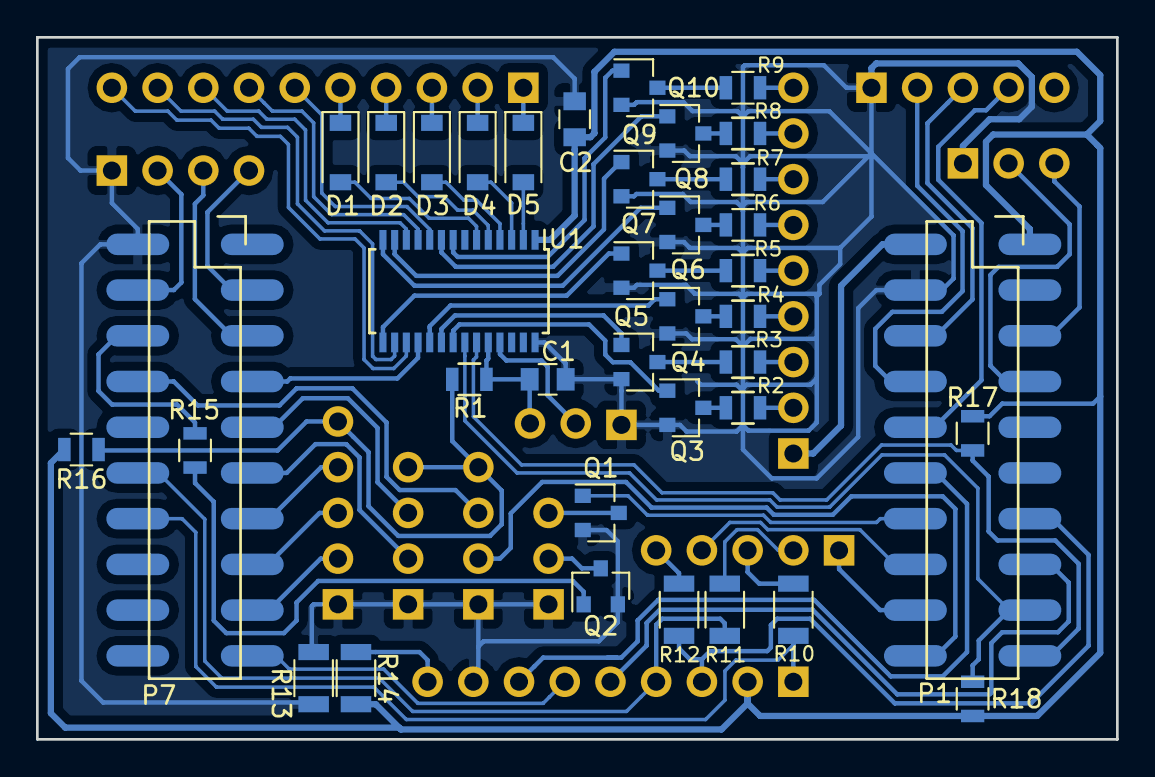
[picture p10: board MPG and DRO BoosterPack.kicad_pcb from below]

Board: 2 copper layers, 60.0 x 39.0 mm, 50 parts (38 on the bottom side), 78 nets.

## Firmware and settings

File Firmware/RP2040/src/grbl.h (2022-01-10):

/*
  config.h - compile time configuration, see note below
  Part of Grbl

  Copyright (c) 2019 Terje Io
  Copyright (c) 2012-2016 Sungeun K. Jeon for Gnea Research LLC
  Copyright (c) 2009-2011 Simen Svale Skogsrud

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
  You should have received a copy of the GNU General Public License
  along with Grbl.  If not, see <http://www.gnu.org/licenses/>.
*/

// NOTE: This file contains parts of config.h copied from grbl for use by MPG/DRO processor

// Define realtime command special characters. These characters are 'picked-off' directly from the
// serial read data stream and are not passed to the grbl line execution parser. Select characters
// that do not and must not exist in the streamed g-code program. ASCII control characters may be
// used, if they are available per user setup. Also, extended ASCII codes (>127), which are never in
// g-code programs, maybe selected for interface programs.
// NOTE: If changed, manually update help message in report.c.

#ifndef __grbl_h__
#define __grbl_h__

#define CMD_EXIT 0x03 // ctrl-C
#define CMD_RESET 0x18 // ctrl-X
#define CMD_STOP 0x19 // ctrl-Y
#define CMD_STATUS_REPORT_LEGACY '?'
#define CMD_CYCLE_START_LEGACY '~'
#define CMD_FEED_HOLD_LEGACY '!'

#define CMD_STATUS_REPORT 0x80
#define CMD_CYCLE_START 0x81
#define CMD_FEED_HOLD 0x82
#define CMD_SAFETY_DOOR 0x84
#define CMD_JOG_CANCEL  0x85
#define CMD_STATUS_REPORT_ALL 0x87

// NOTE: All override realtime commands must be in the extended ASCII character set, starting
// at character value 128 (0x80) and up to 255 (0xFF). If the normal set of realtime commands,
// such as status reports, feed hold, reset, and cycle start, are moved to the extended set
// space, protocol.c's protocol_process_realtime() will need to be modified to accomodate the change.
#define CMD_SAFETY_DOOR 0x84
#define CMD_JOG_CANCEL 0x85
#define CMD_OPTIONAL_STOP_TOGGLE 0x88
#define CMD_SINGLE_BLOCK_TOGGLE 0x89
#define CMD_OVERRIDE_FAN0_TOGGLE 0x8A        // Toggle Fan 0 on/off, not implemented by the core.
#define CMD_MPG_MODE_TOGGLE 0x8B             // Toggle MPG mode on/off, not implemented by the core.
#define CMD_FEED_OVR_RESET 0x90         // Restores feed override value to 100%.
#define CMD_OVERRIDE_FEED_COARSE_PLUS 0x91
#define CMD_OVERRIDE_FEED_COARSE_MINUS 0x92
#define CMD_OVERRIDE_FEED_FINE_PLUS 0x93
#define CMD_OVERRIDE_FEED_FINE_MINUS 0x94
#define CMD_OVERRIDE_RAPID_RESET 0x95        // Restores rapid override value to 100%.
#define CMD_OVERRIDE_RAPID_MEDIUM 0x96
#define CMD_OVERRIDE_RAPID_LOW 0x97
#define CMD_OVERRIDE_SPINDLE_RESET 0x99      // Restores spindle override value to 100%.
#define CMD_OVERRIDE_SPINDLE_COARSE_PLUS 0x9A
#define CMD_OVERRIDE_SPINDLE_COARSE_MINUS 0x9B
#define CMD_OVERRIDE_SPINDLE_FINE_PLUS 0x9C
#define CMD_OVERRIDE_SPINDLE_FINE_MINUS 0x9D
#define CMD_OVERRIDE_SPINDLE_STOP 0x9E
#define CMD_OVERRIDE_COOLANT_FLOOD_TOGGLE 0xA0
#define CMD_OVERRIDE_COOLANT_MIST_TOGGLE 0xA1
#define CMD_TOOL_ACK 0xA3
#define CMD_PROBE_CONNECTED_TOGGLE 0xA4

// Configure rapid, feed, and spindle override settings. These values define the max and min
// allowable override values and the coarse and fine increments per command received. Please
// note the allowable values in the descriptions following each define.
#define DEFAULT_FEED_OVERRIDE           100 // 100%. Don't change this value.
#define MAX_FEED_RATE_OVERRIDE          200 // Percent of programmed feed rate (100-255). Usually 120% or 200%
#define MIN_FEED_RATE_OVERRIDE           10 // Percent of programmed feed rate (1-100). Usually 50% or 1%
#define FEED_OVERRIDE_COARSE_INCREMENT   10 // (1-99). Usually 10%.
#define FEED_OVERRIDE_FINE_INCREMENT      1 // (1-99). Usually 1%.

#define DEFAULT_RAPID_OVERRIDE  100 // 100%. Don't change this value.
#define RAPID_OVERRIDE_MEDIUM    50 // Percent of rapid (1-99). Usually 50%.
#define RAPID_OVERRIDE_LOW       25 // Percent of rapid (1-99). Usually 25%.

#define SPINDLE_NPWM_PIECES                 4 // Maximum number of pieces for spindle RPM linearization, do not change unless more are needed.
#define DEFAULT_SPINDLE_RPM_OVERRIDE      100 // 100%. Don't change this value.
#define MAX_SPINDLE_RPM_OVERRIDE          200 // Percent of programmed spindle speed (100-255). Usually 200%.
#define MIN_SPINDLE_RPM_OVERRIDE           10 // Percent of programmed spindle speed (1-100). Usually 10%.
#define SPINDLE_OVERRIDE_COARSE_INCREMENT  10 // (1-99). Usually 10%.
#define SPINDLE_OVERRIDE_FINE_INCREMENT     1 // (1-99). Usually 1%.

#define MAX_STORED_LINE_LENGTH 80

typedef enum {
    Setting_PulseMicroseconds = 0,
    Setting_StepperIdleLockTime = 1,
    Setting_StepInvertMask = 2,
    Setting_DirInvertMask = 3,
    Setting_InvertStepperEnable = 4,
    Setting_LimitPinsInvertMask = 5,
    Setting_InvertProbePin = 6,
    Setting_StatusReportMask = 10,
    Setting_JunctionDeviation = 11,
    Setting_ArcTolerance = 12,
    Setting_ReportInches = 13,
    Setting_ControlInvertMask = 14,
    Setting_CoolantInvertMask = 15,
    Setting_SpindleInvertMask = 16,
    Setting_ControlPullUpDisableMask = 17,
    Setting_LimitPullUpDisableMask = 18,
    Setting_ProbePullUpDisable = 19,
    Setting_SoftLimitsEnable = 20,
    Setting_HardLimitsEnable = 21,
    Setting_HomingEnable = 22,
    Setting_HomingDirMask = 23,
    Setting_HomingFeedRate = 24,
    Setting_HomingSeekRate = 25,
    Setting_HomingDebounceDelay = 26,
    Setting_HomingPulloff = 27,
    Setting_G73Retract = 28,
    Setting_PulseDelayMicroseconds = 29,
    Setting_RpmMax = 30,
    Setting_RpmMin = 31,
    Setting_LaserMode = 32, // TODO: rename - shared with lathe mode
    Setting_PWMFreq = 33,
    Setting_PWMOffValue = 34,
    Setting_PWMMinValue = 35,
    Setting_PWMMaxValue = 36,
    Setting_StepperDeenergizeMask = 37,
    Setting_SpindlePPR = 38,
    Setting_EnableLegacyRTCommands = 39,

    Setting_HomingLocateCycles = 43,
    Setting_HomingCycle_1 = 44,
    Setting_HomingCycle_2 = 45,
    Setting_HomingCycle_3 = 46,
    Setting_HomingCycle_4 = 47,
    Setting_HomingCycle_5 = 48,
    Setting_HomingCycle_6 = 49,
// Optional driver implemented settings for jogging
    Setting_JogStepSpeed = 50,
    Setting_JogSlowSpeed = 51,
    Setting_JogFastSpeed = 52,
    Setting_JogStepDistance = 53,
    Setting_JogSlowDistance = 54,
    Setting_JogFastDistance = 55,
//
    Setting_RestoreOverrides = 60,
    Setting_IgnoreDoorWhenIdle = 61,
    Setting_SleepEnable = 62,
    Setting_DisableLaserDuringHold = 63,
    Setting_ForceInitAlarm = 64,
    Setting_CheckLimitsAtInit = 65,
    Setting_HomingInitLock = 66,
    Settings_Stream = 70,
// Optional settings for closed loop spindle speed control
    Setting_SpindlePGain = 80,
    Setting_SpindleIGain = 81,
    Setting_SpindleDGain = 82,
    Setting_SpindleDeadband = 83,
    Setting_SpindleMaxError = 84,
    Setting_SpindleIMaxError = 85,
    Setting_SpindleDMaxError = 86,

// Optional settings for closed loop spindle synchronized motion
    Setting_PositionPGain = 90,
    Setting_PositionIGain = 91,
    Setting_PositionDGain = 92,
    Setting_PositionDeadband = 93,
    Setting_PositionMaxError = 94,
    Setting_PositionIMaxError = 95,
    Setting_PositionDMaxError = 96,
//

    Setting_AxisSettingsBase = 100, // NOTE: Reserving settings values >= 100 for axis settings. Up to 255.
    Setting_AxisSettingsMax = 255
} setting_type_t;

#endif

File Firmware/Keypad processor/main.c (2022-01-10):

//
// Keypad handler with partial 2-key rollover, autorepeat and I2C interface
//
// Target: MSP430G2553
//
// v2.0 / 2022-01-09 / Io Engineering / Terje
//

/*

Copyright (c) 2017-2022, Terje Io
All rights reserved.

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
· Redistributions of source code must retain the above copyright notice, this
list of conditions and the following disclaimer.

· Redistributions in binary form must reproduce the above copyright notice, this
list of conditions and the following disclaimer in the documentation and/or
other materials provided with the distribution.

· Neither the name of the copyright holder nor the names of its contributors may
be used to endorse or promote products derived from this software without
specific prior written permission.

THIS SOFTWARE IS PROVIDED BY THE COPYRIGHT HOLDERS AND CONTRIBUTORS "AS IS" AND
ANY EXPRESS OR IMPLIED WARRANTIES, INCLUDING, BUT NOT LIMITED TO, THE IMPLIED
WARRANTIES OF MERCHANTABILITY AND FITNESS FOR A PARTICULAR PURPOSE ARE
DISCLAIMED. IN NO EVENT SHALL THE COPYRIGHT OWNER OR CONTRIBUTORS BE LIABLE FOR
ANY DIRECT, INDIRECT, INCIDENTAL, SPECIAL, EXEMPLARY, OR CONSEQUENTIAL DAMAGES
(INCLUDING, BUT NOT LIMITED TO, PROCUREMENT OF SUBSTITUTE GOODS OR SERVICES;
LOSS OF USE, DATA, OR PROFITS; OR BUSINESS INTERRUPTION) HOWEVER CAUSED AND ON
ANY THEORY OF LIABILITY, WHETHER IN CONTRACT, STRICT LIABILITY, OR TORT
(INCLUDING NEGLIGENCE OR OTHERWISE) ARISING IN ANY WAY OUT OF THE USE OF THIS
SOFTWARE, EVEN IF ADVISED OF THE POSSIBILITY OF SUCH DAMAGE.

*/

#include <msp430.h> 

#include <stdint.h>
#include <stdbool.h>
#include <string.h>

#define I2CADDRESS 0x49

#define MAP_4X4_EMPTY   0
#define MAP_5X5_EMPTY   1
#define MAP_4X4_DEFAULT 2
#define MAP_5X5_DEFAULT 3
#define MAP_4X4_CNC     4
#define MAP_5X5_CNC     5
#define MAP_5X5_LEGACY  6

#define N_KEYS_MAX 75
#define DEFAULT_MAP MAP_5X5_CNC
#define MPGKEYS // 5x5 keypad (for grbl MPG & DRO)

#define SCL BIT6    // P1.6 I2C
#define SDA BIT7    // P1.7 I2C

#ifdef MPGKEYS
#define BUTINTR BIT5                        // P2.5
#else
#define BUTINTR BIT4                        // P2.4
#endif

#define BUTDRIVE4 (BIT0|BIT1|BIT2|BIT3)      // P1.0-3
#define BUTINPUT4 (BIT0|BIT1|BIT2|BIT3)      // P2.0-3
#define BUTDRIVE5 (BIT0|BIT1|BIT2|BIT3|BIT4) // P1.0-4
#define BUTINPUT5 (BIT0|BIT1|BIT2|BIT3|BIT4) // P2.0-4

typedef uint8_t keytype_t;

enum keytype_t {
    Keytype_None = 0,
    Keytype_AutoRepeat,
    Keytype_SingleEvent,
    Keytype_LongPress,
    Keytype_Persistent
};

#pragma pack(push, 1)

typedef struct {
    char key;
    keytype_t type;
    uint16_t scanCode;
} key_t;

typedef struct {
    uint8_t n_keys;
    uint8_t rowshift;
    uint8_t drive_mask;
    uint8_t input_mask;
    bool powerkeys;
    uint16_t shift_key;
    key_t key[N_KEYS_MAX];
} keymap_t;

#pragma pack(pop)

char keycode = '\0'; // Keycode to transmit
volatile bool keyclick = false;
bool getpower = false;
unsigned int laserpower = 10;
keymap_t keymap;
struct {
    volatile uint16_t count;
    volatile uint8_t *ptr;
    uint8_t data[4];
} i2c_rx = {0};

static void gpio_init (keymap_t *map, uint8_t input_mask, uint8_t drive_mask)
{
    map->input_mask = input_mask;
    map->drive_mask = drive_mask;

    P2DIR &= ~input_mask;               // P2.x button inputs
    P2OUT &= ~input_mask;               // Enable button input pull downs
    P2REN |= input_mask;                // ...
    P2IES &= ~input_mask;               // and set L-to-H interrupt

    P2IFG = 0;                          // Clear any pending flags
    P2IE |= input_mask;                 // Enable interrupts

    P1DIR |= drive_mask;                // Enable P1 outputs
    P1OUT |= drive_mask;                // for keypad
}

// Keytype_LongPress generates the lower case version of the character on a short keypress, uppercase on a long keypress.
// Keytype_Persistent keeps the strobe pin low as long as the key is pressed.

void map_4x4_empty (void)
{
    memset(&keymap, 0, sizeof(keymap_t));
    keymap.rowshift = 4;

    gpio_init(&keymap, BUTINPUT4, BUTDRIVE4);
}

void map_5x5_empty (void)
{
    memset(&keymap, 0, sizeof(keymap_t));
    keymap.rowshift = 5;

    gpio_init(&keymap, BUTINPUT5, BUTDRIVE5);
}

void map_4x4_default (void)
{
    static const key_t keyMap[] = {
        {0x0B, Keytype_AutoRepeat, 0x11},
        {'9',  Keytype_AutoRepeat, 0x21},
        {'8',  Keytype_AutoRepeat, 0x41},
        {'7',  Keytype_AutoRepeat, 0x81},

        {0x1B, Keytype_AutoRepeat, 0x12},
        {'6',  Keytype_AutoRepeat, 0x22},
        {'5',  Keytype_AutoRepeat, 0x42},
        {'4',  Keytype_AutoRepeat, 0x82},

        {0x18, Keytype_SingleEvent, 0x14},
        {'3',  Keytype_AutoRepeat,  0x24},
        {'2',  Keytype_AutoRepeat,  0x44},
        {'1',  Keytype_AutoRepeat,  0x84},

        {'\r', Keytype_AutoRepeat, 0x18},
        {'-',  Keytype_AutoRepeat, 0x28},
        {'+',  Keytype_AutoRepeat, 0x48},
        {'0',  Keytype_AutoRepeat, 0x88},

    // two key rollover codes
        {'s',  Keytype_AutoRepeat,  0xC3},
        {'t',  Keytype_AutoRepeat,  0xC6},
        {'q',  Keytype_AutoRepeat,  0x63},
        {'r',  Keytype_AutoRepeat,  0x66}
    };

    map_4x4_empty();

    keymap.n_keys = (sizeof(keyMap) / sizeof(key_t));
    memcpy(&keymap.key, keyMap, sizeof(keyMap));
}

void map_5x5_default (void)
{
    static const key_t keyMap[] = {
        {'7',  Keytype_LongPress,   0b0000100001}, //
        {'8',  Keytype_Persistent,  0b0000100010}, //
        {'9',  Keytype_LongPress,   0b0000100100}, //
        {'-',  Keytype_Persistent,  0b0000101000}, //
        {0x7F, Keytype_SingleEvent, 0b0000110000}, // DEL

        {'4',  Keytype_Persistent,  0b0001000001}, //
        {'5',  Keytype_LongPress,   0b0001000010}, //
        {'6',  Keytype_Persistent,  0b0001000100}, //
        {'+',  Keytype_LongPress,   0b0001001000}, //
        {0x08, Keytype_SingleEvent, 0b0001010000}, // BS

        {'1',  Keytype_SingleEvent, 0b0010000001}, //
        {'2',  Keytype_Persistent,  0b0010000010}, //
        {'3',  Keytype_SingleEvent, 0b0010000100}, //
        {'\r', Keytype_Persistent,  0b0010001000}, //
        {0x0B, Keytype_SingleEvent, 0b0010010000}, // VT

        {'0',  Keytype_SingleEvent, 0b0100000001}, //
        {0,    Keytype_SingleEvent, 0b0100000010}, //
        {0,    Keytype_SingleEvent, 0b0100000100}, //
        {0x09, Keytype_SingleEvent, 0b0100001000}, // HT
        {0x0A, Keytype_SingleEvent, 0b0100010000}, // LF

        {128,  Keytype_LongPress,   0b1000000001}, //
        {129,  Keytype_SingleEvent, 0b1000000010}, //
        {0,    Keytype_LongPress,   0b1000000100}, //
        {0,    Keytype_SingleEvent, 0b1000001000}, //
        {0xFF, Keytype_SingleEvent, 0b1000010000}, // Shift
    };

    map_5x5_empty();

    keymap.n_keys = (sizeof(keyMap) / sizeof(key_t));
    keymap.shift_key = 0b1000010000;
    memcpy(&keymap.key, keyMap, sizeof(keyMap));
}

void cnc_map_4x4_default (void)
{
    static const key_t keyMap[] = {
        {0x0B, Keytype_SingleEvent, 0x11},
        {'C',  Keytype_SingleEvent, 0x21},
        {'U',  Keytype_Persistent, 0x41},
        {'M',  Keytype_SingleEvent, 0x81},

        {0x1B, Keytype_SingleEvent, 0x12},
        {'R',  Keytype_Persistent, 0x22},
        {'H',  Keytype_LongPress, 0x42},
        {'L',  Keytype_Persistent, 0x82},

        {'~',  Keytype_SingleEvent, 0x14},
        {'3',  Keytype_SingleEvent,  0x24},
        {'D',  Keytype_Persistent,  0x44},
        {'S',  Keytype_SingleEvent,  0x84},

        {'!',  Keytype_SingleEvent, 0x18},
        {'-',  Keytype_SingleEvent, 0x28},
        {'+',  Keytype_SingleEvent, 0x48},
        {'0',  Keytype_SingleEvent, 0x88},

    // two key rollover codes
        {'s',  Keytype_Persistent,  0xC3},
        {'t',  Keytype_Persistent,  0xC6},
        {'q',  Keytype_Persistent,  0x63},
        {'r',  Keytype_Persistent,  0x66}
    };

    map_4x4_empty();

    keymap.n_keys = (sizeof(keyMap) / sizeof(key_t));
    keymap.powerkeys = true;
    memcpy(&keymap.key, keyMap, sizeof(keyMap));
}

void cnc_map_default (void)
{
    static const key_t keyMap[] = {
        {'A',  Keytype_LongPress,   0b0000100001}, // X lock toggle, X<0>
        {'F',  Keytype_Persistent,  0b0000100010}, // Jog Y+
        {'G',  Keytype_LongPress,   0b0000100100}, // Y lock toggle, Y<0>
        {'U',  Keytype_Persistent,  0b0000101000}, // Jog Z+
        {'\r', Keytype_SingleEvent, 0b0000110000}, // MPG mode toggle

        {'L',  Keytype_Persistent,  0b0001000001}, // Jog X-
        {'H',  Keytype_LongPress,   0b0001000010}, // Jog mode toggle (step, slow, fast), Home
        {'R',  Keytype_Persistent,  0b0001000100}, // Jog X+
        {'E',  Keytype_LongPress,   0b0001001000}, // Z lock toggle, Z<0>
        {'~',  Keytype_SingleEvent, 0b0001010000}, // Cycle Start

        {'M',  Keytype_SingleEvent, 0b0010000001}, // Mist coolant toogle
        {'B',  Keytype_Persistent,  0b0010000010}, // Jog Y-
        {'C',  Keytype_SingleEvent, 0b0010000100}, // Flood coolant toogle
        {'D',  Keytype_Persistent,  0b0010001000}, // Jog Z-
        {'!',  Keytype_SingleEvent, 0b0010010000}, // Feed hold

        {'m',  Keytype_SingleEvent, 0b0100000001}, // X MPG scale factor toggle
        {'n',  Keytype_SingleEvent, 0b0100000010}, // Y MPG scale factor toggle
        {'o',  Keytype_SingleEvent, 0b0100000100}, // Z MPG scale factor toggle
        {'T',  Keytype_SingleEvent, 0b0100001000}, // Toggle MPG axis (X, Y, Z)
        {'s',  Keytype_SingleEvent, 0b0100010000}, // Spindle on/off toogle

        {'I',  Keytype_LongPress,   0b1000000001}, // Feed rate override +10%, feed rate override reset
        {'j',  Keytype_SingleEvent, 0b1000000010}, // Feed rate override -10%
        {'K',  Keytype_LongPress,   0b1000000100}, // Spindle RPM override +10%, spindle RPM override reset
        {'z',  Keytype_SingleEvent, 0b1000001000}, // Spindle RPM override -10%
        {0xFF, Keytype_SingleEvent, 0b1000010000}, // Shift
    // two key rollover codes
        {'r',  Keytype_Persistent,  0b0001000100|0b0000100010}, // R + F: Jog X+Y+
        {'q',  Keytype_Persistent,  0b0001000100|0b0010000010}, // R + B: Jog X+Y-
        {'s',  Keytype_Persistent,  0b0001000001|0b0000100010}, // L + F: Jog X-Y+
        {'t',  Keytype_Persistent,  0b0001000001|0b0010000010}, // L + B: Jog X-Y-
        {'w',  Keytype_Persistent,  0b0001000100|0b0000101000}, // R + U: Jog X+Z+
        {'v',  Keytype_Persistent,  0b0001000100|0b0010001000}, // R + D: Jog X+Z-
        {'u',  Keytype_Persistent,  0b0001000001|0b0000101000}, // L + U: Jog X-Z+
        {'x',  Keytype_Persistent,  0b0001000001|0b0010001000}, // L + D: Jog X-Z-
        {0x93, Keytype_SingleEvent, 0b1000010000|0b1000000001}, // Shift + I: Feed rate override +1%
        {0x94, Keytype_SingleEvent, 0b1000010000|0b1000000010}, // Shift + j: Feed rate override -1%
        {0x9C, Keytype_SingleEvent, 0b1000010000|0b1000000100}, // Shift + K: Spindle RPM override +1%
        {0x9D, Keytype_SingleEvent, 0b1000010000|0b1000001000}, // Shift + z: Spindle RPM override -1%
    };

    map_5x5_empty();

    keymap.n_keys = (sizeof(keyMap) / sizeof(key_t));
    keymap.shift_key = 0b1000010000;
    memcpy(&keymap.key, keyMap, sizeof(keyMap));
}

void cnc_map_legacy (void)
{
    static const key_t keyMap[] = {
        {'\r', Keytype_SingleEvent, 0x0101}, // MPG mode toggle
        {'C',  Keytype_SingleEvent, 0x0201}, // Flood coolant toogle
        {'R',  Keytype_Persistent,  0x0401}, // Right (X+)
        {'.',  Keytype_SingleEvent, 0x0801},
        {'.',  Keytype_SingleEvent, 0x1001}, // Shift

        {'~',  Keytype_SingleEvent, 0x0102}, // Cycle Start
        {'S',  Keytype_SingleEvent, 0x0202}, // Spindle on/off toogle
        {'.',  Keytype_SingleEvent, 0x0402},
        {'U',  Keytype_Persistent,  0x0802}, // Up (Z+)
        {'.',  Keytype_SingleEvent, 0x1002},

        {'E',  Keytype_LongPress,   0x0104}, // Z lock
        {'m',  Keytype_SingleEvent, 0x0204}, // X factor
        {'.',  Keytype_SingleEvent, 0x0404},
        {'.',  Keytype_SingleEvent, 0x0804},
        {'L',  Keytype_Persistent,  0x1004}, // Left (X-)

        {'!',  Keytype_SingleEvent, 0x0108}, // Feed hold
        {'M',  Keytype_SingleEvent, 0x0208}, // Mist coolant toogle
        {'F',  Keytype_Persistent,  0x0408},
        {'.',  Keytype_SingleEvent, 0x0808},
        {'H',  Keytype_LongPress,   0x1008}, // Jog toggle / Home

        {'o',  Keytype_SingleEvent, 0x0110}, // Z factor
        {'A',  Keytype_LongPress,   0x0210}, // X lock
        {'.',  Keytype_SingleEvent, 0x0410},
        {'.',  Keytype_SingleEvent, 0x0810},
        {'D',  Keytype_Persistent,  0x1010}, // Down (Z-),
    // two key rollover codes
        {'s',  Keytype_Persistent,  0x0C03}, // R + U
        {'r',  Keytype_Persistent,  0x1411}, // D + R
        {'q',  Keytype_Persistent,  0x1806}, // L + U
        {'t',  Keytype_Persistent,  0x1014}, // D + L
        {'.',  Keytype_SingleEvent, 0xC502},
        {'.',  Keytype_SingleEvent, 0b0000011111}
    };

    map_5x5_empty();

    keymap.n_keys = (sizeof(keyMap) / sizeof(key_t));
    keymap.rowshift = 8;
    memcpy(&keymap.key, keyMap, sizeof(keyMap));
}

void select_map (uint8_t map)
{
    switch(map) {

        case MAP_4X4_EMPTY:
            map_4x4_empty();
            break;

        case MAP_5X5_EMPTY:
            map_5x5_empty();
            break;

        case MAP_4X4_DEFAULT:
            map_4x4_default();
            break;

        case MAP_5X5_DEFAULT:
            map_5x5_default();
            break;

        case MAP_4X4_CNC:
            cnc_map_4x4_default();
            break;

        case MAP_5X5_CNC:
            cnc_map_default();
            break;

        case MAP_5X5_LEGACY:
            cnc_map_legacy();
            break;
    }
}

// System Routines

const key_t *keyscan (void);

void initI2C (void)
{
    P1SEL  |= SCL|SDA;              // Assign I2C pins to
    P1SEL2 |= SCL|SDA;              // USCI_B0 (P1)

    IE2 &= ~UCB0TXIE;               // Disable TX interrupt
    UCB0CTL1 |= UCSWRST;            // Enable SW reset
    UCB0CTL0 = UCMODE_3|UCSYNC;     // I2C Slave, synchronous mode
    UCB0I2COA = I2CADDRESS;         // Own Address is 048h
    UCB0CTL1 &= ~UCSWRST;           // Clear SW reset, resume operation
    UCB0I2CIE |= UCSTPIE| UCSTTIE;  // Enable STT, STP and
    IE2 |= UCB0RXIE|UCB0TXIE;       // RX/TX interrupts
}

void sleep (uint16_t time)
{
    TA0CTL |= TACLR;    // Clear timer and
    TA0CCR0 = time;     // set sleep duration
    TA0CTL |= MC0;      // Start timer in up mode and
    LPM0;               // sleep until times out...
}

const key_t *debounce (char key)
{
    const key_t *keypress;

    while((keypress = keyscan()) && keypress->key != key) { // Scan keys
        sleep(5000);                                        // until result
        key = keypress->key;                                // settles
    }

    return keypress;
}

void main (void)
{
    volatile char lastkey;
    uint_fast16_t autorepeat;
    bool longPress = false;
    const key_t *keypress;

    DCOCTL = 0;
    WDTCTL = WDTPW+WDTHOLD;             // Stop watchdog timer
    DCOCTL = CALDCO_16MHZ;              // Set DCO for 16MHz using
    BCSCTL1 = CALBC1_16MHZ;             // calibration registers
    BCSCTL2 = DIVS0|DIVS1;              // SMCLK = MCLK / 8

    TA0CTL |= TACLR|TASSEL1|ID0|ID1;    // SMCLK/8, Clear TA
    TA0CCTL0 |= CCIE;                   // Enable CCR0 interrupt

    _EINT();                            // Enable interrupts

    sleep(50);

    initI2C();

    P3DIR = 0xFF;                       // Set P3 pins to outputs
    P3OUT = 0xFF;                       // and set high

    select_map(DEFAULT_MAP);

    while(1) {

        keycode = '\0';
        keyclick = false;
        P1OUT |= keymap.drive_mask;                 // Drive all rows high
        P2DIR &= ~BUTINTR;                          // and clear button strobe (keydown, set to high-Z)
        P2IFG = 0;                                  // Clear any pending flags

        sleep(10000);                               // Wait a bit for things to settle

        if(!(P2IN & keymap.input_mask) || keypress->scanCode == keymap.shift_key) {                    // No key pressed?
            keypress = 0;
            P2IE |= keymap.input_mask;              // Yes, enable interrupts and
            LPM0;                                   // sleep until key pressed

            P2IE &= ~keymap.input_mask;             // Disable interrupts
        }

        sleep(10000);                               // Wait a bit for things to settle

        if(keyclick && (keypress = keyscan()))      // Key still pressed?
            keypress = debounce(keypress->key);     // Yep, debounce to ensure stable result

        if(keypress) {

            lastkey = '\0';
            autorepeat = 0;
            longPress = false;

            do {

                if(lastkey && keypress->key != lastkey) { // Key change?

                    keycode = '\0';
                    autorepeat = 0;
                    longPress = false;

                    if(P2DIR & BUTINTR) {   // for persistent key?
                        P2DIR &= ~BUTINTR;  // terminate key pressed signal
                        sleep(200);         // and sleep a little (0.8 mS)
                    }
                }

                switch(keypress->type) {

                    case Keytype_LongPress:
                        keycode = keypress->key;
                        longPress = true;
                        autorepeat++;
                        sleep(64000);
                        break;

                    case Keytype_AutoRepeat:
                        keycode = keypress->key;
                        P2DIR |= BUTINTR;
                        P2OUT &= ~BUTINTR;
                        sleep(50); // 200 us
                        P2DIR &= ~BUTINTR;
                        autorepeat++;
                        sleep(autorepeat < 2 ? 64000 : 10000);
                        break;

                    case Keytype_Persistent:
                        keycode = keypress->key;
                        P2DIR |= BUTINTR;
                        P2OUT &= ~BUTINTR;
                        break;

                    default:
                        if(lastkey != keypress->key) {
                            keycode = keypress->key;
                            P2DIR |= BUTINTR;
                            P2OUT &= ~BUTINTR;
                            sleep(50); // 200 us
                            P2DIR &= ~BUTINTR;
                        }
                        break;
                }

                lastkey = keypress->key;

                if(keymap.powerkeys) switch(keycode) {

                    case '-':
                        if(laserpower > 0)
                            laserpower--;
                        break;

                    case '+':
                        if(laserpower < 100)
                            laserpower++;
                        break;
                }

                sleep(5000); // Wait for ~20 ms before transmitting again

                if(keypress->scanCode == keymap.shift_key)
                    break;

            } while((keypress = debounce(lastkey))); // Keep transmitting while button(s) held down

            if(keymap.powerkeys && (lastkey == '-' || lastkey == '+')) {
                keycode = 'P';
                P2DIR |= BUTINTR;
                P2OUT &= ~BUTINTR;
                sleep(50); // 200 us
            } else if(longPress) { // lowercaps key
                keycode = autorepeat < 5 ? lastkey | 0x20 : lastkey;
                P2DIR |= BUTINTR;
                P2OUT &= ~BUTINTR;
                sleep(50); // 200 us
            }
            P2DIR &= ~BUTINTR;                      // Clear button strobe
        }
    }
}

const key_t *keyscan (void)
{
    uint16_t scancode = 0;                          // Initialize scancode and
    uint16_t index = BIT0;                          // row mask

    if(!(P2IN & keymap.input_mask))                 // Keys still pressed?
        return 0;                                   // no, exit

    while(index & keymap.drive_mask) {              // Loop through all rows

        P1OUT &= ~keymap.drive_mask;                // Stop driving rows

        P2DIR |= keymap.input_mask;                 // Temporarily set column pins to output
        P2OUT &= ~keymap.input_mask;                // and switch low to bleed off charge
        P2DIR &= ~keymap.input_mask;                // in order to avoid erroneous reads
        P2OUT &= ~keymap.input_mask;                // Enable pull down resistors
        P2REN |= keymap.input_mask;                 // on column inputs

        P1OUT |= index;                             // Drive row

        __delay_cycles(16);

        if(P2IN & keymap.input_mask) {              // If any key pressed:
            scancode |= (index << keymap.rowshift); // set bit for row scanned
            scancode |= (P2IN & keymap.input_mask); // set bit(s) for column(s)
        }

        index = index << 1;                         // Next row
    }

    P1OUT |= keymap.drive_mask;                     // Drive all rows high again

    index = keymap.n_keys;

    if(scancode != 0)                                               // If key(s) were pressed
        while(index && keymap.key[--index].scanCode != scancode);   // then try to resolve to legal entry in lookup table

    return scancode != 0 && keymap.key[index].scanCode == scancode ? &keymap.key[index] : 0;
}
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

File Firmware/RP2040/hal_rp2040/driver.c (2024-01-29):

/*
 * driver.c - HAL driver for Raspberry RP2040 ARM processor
 *
 * Part of MPG/DRO for grbl on a secondary processor
 *
 * v0.0.4 / 2023-03-04 / (c) Io Engineering / Terje
 */

/*

Copyright (c) 2021-2023, Terje Io
All rights reserved.

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
* Neither the name of the copyright holder nor the names of its contributors may
be used to endorse or promote products derived from this software without
specific prior written permission.

THIS SOFTWARE IS PROVIDED BY THE COPYRIGHT HOLDERS AND CONTRIBUTORS "AS IS" AND
ANY EXPRESS OR IMPLIED WARRANTIES, INCLUDING, BUT NOT LIMITED TO, THE IMPLIED
WARRANTIES OF MERCHANTABILITY AND FITNESS FOR A PARTICULAR PURPOSE ARE
DISCLAIMED. IN NO EVENT SHALL THE COPYRIGHT OWNER OR CONTRIBUTORS BE LIABLE FOR
ANY DIRECT, INDIRECT, INCIDENTAL, SPECIAL, EXEMPLARY, OR CONSEQUENTIAL DAMAGES
(INCLUDING, BUT NOT LIMITED TO, PROCUREMENT OF SUBSTITUTE GOODS OR SERVICES;
LOSS OF USE, DATA, OR PROFITS; OR BUSINESS INTERRUPTION) HOWEVER CAUSED AND ON
ANY THEORY OF LIABILITY, WHETHER IN CONTRACT, STRICT LIABILITY, OR TORT
(INCLUDING NEGLIGENCE OR OTHERWISE) ARISING IN ANY WAY OUT OF THE USE OF THIS
SOFTWARE, EVEN IF ADVISED OF THE POSSIBILITY OF SUCH DAMAGE.

*/

#include "pico/stdlib.h"
#include "hardware/i2c.h"
#include "hardware/gpio.h"
#include "hardware/irq.h"
#include "hardware/structs/systick.h"

#include "../src/grbl/grbl.h"
#include "../src/config.h"
#include "../src/interface.h"

#include "i2c_nb.h"
#include "driver.h"

static leds_t leds_state = {
    .value = 255
};

#if UILIB_KEYPAD_ENABLE

#include "../src/keypad.h"

#define SHIFT_KEY 0b1000010000

static bool keyDown = false;
static void keyclick_int_handler (uint gpio, uint32_t events);

static const keypad_key_t kmap[] = {
    { .key = CMD_STOP, .type = Keytype_SingleEvent, .scanCode = SHIFT_KEY|0b0100000001 }
/*    { .key = '4', .type = Keytype_SingleEvent, .scanCode = SHIFT_KEY|0b0100000001 },
    { .key = '5', .type = Keytype_SingleEvent, .scanCode = SHIFT_KEY|0b0100000010 },
    { .key = '6', .type = Keytype_SingleEvent, .scanCode = SHIFT_KEY|0b0100000100 } */
};

#endif

#if UILIB_NAVIGATOR_ENABLE

#include "encoder.pio.h"

static void encoder_int_handler (void);
static void nav_sw_int_handler (uint gpio, uint32_t events);
static void mpg_int_handler (void);

static qei_t qei = {0}, qei_mpg;
static mpg_t mpg = {0};
static mpg_axis_t *mpg_axis;

static int enc_sm, mpg_sm;

#define LAST_STATE(state)  ((state) & 0b0011)
#define CURR_STATE(state)  (((state) & 0b1100) >> 2)

static const uint32_t STATE_A_MASK      = 0x80000000;
static const uint32_t STATE_B_MASK      = 0x40000000;
static const uint32_t STATE_A_LAST_MASK = 0x20000000;
static const uint32_t STATE_B_LAST_MASK = 0x10000000;

#define STATES_MASK (STATE_A_MASK | STATE_B_MASK | STATE_A_LAST_MASK | STATE_B_LAST_MASK);

static const uint32_t TIME_MASK   = 0x0fffffff;

static const uint8_t MICROSTEP_0  = 0b00;
static const uint8_t MICROSTEP_1  = 0b10;
static const uint8_t MICROSTEP_2  = 0b11;
static const uint8_t MICROSTEP_3  = 0b01;

#endif
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

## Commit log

2018-05-03 MPG and DRO BoosterPack for Texas Instruments Tiva C
    For eliminating a cable mess and providing ample I/O for keys (buttons)
    and LEDs, has an onboard MSP430G2553 for that.
    [MPG and DRO BoosterPack.kicad_pcb, MPG and DRO BoosterPack.sch]
2018-10-17 Added link to required display drivers library
2019-04-17 Some code cleanup, added spindle RPM control
    Spindle RPM can now be adjusted with navigator (Menu encoder) when DRO
    canvas is active. Min/max RPM limits are read from grbl settings on
    connect.
2019-06-03 Many improvements in grbl message parser++
    Some improvements needs my grblHAL port to function correctly as my
    forked vanilla grbl lacks good support for MPG. Among lacking features
    are message output synced to gcode execution and the fact that execution
    continues after an error (until the sender stops transmitting and the
    input buffer is empty - depends on streaming mode). The latest grbHAL
    version (to be updated soon) will return the last error until a reset, a
    stop, a system command or a buffer flush is issued by the sender.
    [dro.c, grbl.h, grblcomm.c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]
2019-08-21 Improved startup sequence, added detection/handling of grbl resets.
    [grbl.h, grblcomm.c, grblcomm.h]
2021-08-30 Added preliminary Pi Pico board design
    [MPG and DRO BoosterPack.kicad_pcb, MPG and DRO BoosterPack.sch]
2021-08-30 Added Pi Pico design files
    [RP2040 MPG and DRO.kicad_pcb, RP2040 MPG and DRO.sch]
2022-01-10 Updated to new structure, added RP2040 (Pi Pico) firmware
2022-01-13 Added default keys and LEDs wiring diagram, updated readme
2023-02-06 Bug fixes, issue #13
    [driver.c, dro.c, serial.c]
2023-02-27 Added pin label for clarity
2025-03-09 Updated to latest version. Fix for changed compiler optimization causing font render failure.
    [dro.c, grbl.h, grblcomm.c]

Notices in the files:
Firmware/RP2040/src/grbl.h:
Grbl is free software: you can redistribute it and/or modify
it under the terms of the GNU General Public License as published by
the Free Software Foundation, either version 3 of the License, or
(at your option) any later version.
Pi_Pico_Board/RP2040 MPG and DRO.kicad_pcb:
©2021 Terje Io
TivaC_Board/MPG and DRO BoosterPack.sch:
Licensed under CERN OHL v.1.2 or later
